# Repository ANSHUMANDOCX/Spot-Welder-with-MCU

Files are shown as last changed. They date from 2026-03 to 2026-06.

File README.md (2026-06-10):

# Spot Welder with MCU
## Description
- This is a Mosfet Based Spot welder made using IRFB7430 mosfet paired with a OLED display, rotary encoder and ATMEGA328P IC. This is a projet inspired by [This Project](https://www.instructables.com/DIY-Arduino-Battery-Spot-Welder/) 
- This is a two PCB Design and made such that one can order the PCB as a whole and has to separate the PCBs by Cutting manually to save cost.
- It has two Aluminum parts that attach to the PCB since the circuit will be dealing high current of about 400A in a single pulse
- The pulse timing can be adjusted using the rotary encode and is very simple to use.
- It has a onboard programmer for the ease of programming the board
- Flash using Arduino IDE with ATmega328P bootloader and 9600 baud rate
- The Code is not tested yet on my design
## Parts used 
- IRFB7430 Mosfet
- Atmega328p as the MCU 
- 0.96 128x64 oled display
- ABR-PR-12APBTX90 Amaron 12v 9Ah Battey for high short pulse current
- 6AWG wire to handle the high current
- 4010 fan 
- 2mm solid copper wire
## Usage guide 
We need to connect the GND of the Battery from the IN sign and connect to the U shaped aluminium portion followed by the rectangular aluminium block as one of the probes the other probe will the positive terminal of the battery.
## PCB Schematic and CAD 







## Build 
WhatsApp Image 2026-06-11 at 12 53 13 AM
WhatsApp Image 2026-06-11 at 12 53 09 AM
WhatsApp Image 2026-06-11 at 12 53 09 AM (1)
WhatsApp Image 2026-06-11 at 12 53 10 AM
WhatsApp Image 2026-06-11 at 12 53 10 AM (2)
WhatsApp Image 2026-06-11 at 12 53 10 AM (3)
WhatsApp Image 2026-06-11 at 12 53 11 AM (1)
WhatsApp Image 2026-06-11 at 12 53 11 AM (2)
https://drive.google.com/file/d/1lwMrrw48pk1E9WbPoM3kms2gutVuB4EL/view?usp=sharing

## BOM 
| Name | Purpose | Cost Per Item (USD) | Quantity | Total (USD) | Link | Distributor |
|---|---|---|---|---|---|---|
| SHIPPING JLC+LCSC | SHIPPING | 10.00 | 1 | 10.00 | [LINK](https://lcsc.com) | LCSC, JLC |
| Aluminum parts+ PCB | PCB + Aluminum Block | 6.00 | 1 | 6.00 | [LINK](https://jlccnc.com) | JLCCNC, JLCPCB  |
| FAN | to disspate heat | 0.70 | 1 | 0.70 | [LINK](https://makerbazar.in/products/generic-axial-dc-cooling-fan-blowers?variant=46306240004336) | Maker Bazar |
| Passive Component | Resistor diodes and Capacitor | 6.06 | 1 | 6.06 | [LINK](https://lcsc.com) | LCSC |
| 6AWG wire | Heavy duty wires | 4.73 | 1 | 4.73 | [LINK](https://makerbazar.in/products/flexible-silicon-wire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) | Maker Bazar |
| Battery 9ah | the battery | 18.25 | 1 | 18.25 | [LINK](https://www.flipkart.com/amaron-abr-pr-12apbtx90-9-ah-battery-bike/p/itmd23986a4bee47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,1,G,11214002,x,,,,,,,c,,,,,,,&entryMethod=22371611432&&cmpid=content_22371611432_gmc_pla&gad_campaignid=22371673895) | Flipkart |
| MCP1407-E/SN | gate driver | 1.75 | 1 | 1.75 | [LINK](https://www.lcsc.com/product-detail/C52138.html) | LCSC |
| 5.0SMDJ13A | diode | 0.42 | 4 | 1.70 | [LINK](https://www.lcsc.com/product-detail/C5295091.html) | LCSC |
| IRFB7430PBF(UMW) | Mosfets | 0.44 | 10 | 4.43 | [LINK](https://www.lcsc.com/product-detail/C19100591.html) | LCSC |
| CH340K | USB UART | 0.62 | 1 | 0.62 | [LINK](https://www.lcsc.com/product-detail/C968586.html) | LCSC |
| Oled | to show the timer | 2.17 | 1 | 2.17 | [LINK](https://www.lcsc.com/product-detail/C5248080.html) | LCSC |
| Rotary encoder | to set the timer | 1.42 | 1 | 1.42 | [LINK](https://www.lcsc.com/product-detail/C19712528.html) | LCSC |
| 3.3uH 20mΩ Inductor | Inductor | 0.71 | 1 | 0.71 | [LINK](https://www.lcsc.com/product-detail/C7588932.html) | LCSC |
| TPS563201DDCT | Regulator | 0.46 | 1 | 0.46 | [LINK](https://www.lcsc.com/product-detail/C2070819.html) | LCSC |
| ATMEGA328P-AU | MCU | 2.17 | 1 | 2.17 | [LINK](https://www.lcsc.com/product-detail/C14877.html) | LCSC |
| **Grand Total** | | | | **63.17** | | |

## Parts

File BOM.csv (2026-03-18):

Index | LCSC# | MPN | Manufacturer | Package | Customer # | Description | RoHS | Quantity | MOQ | Multiple | Unit Price($) | Extended Price($) | Product Link
1 | C14877 | ATMEGA328P-AU | MICROCHIP | TQFP-32(7x7) |  | AVR 8 Bit 20MHz 23 TQFP-32(7x7) Microcontrollers RoHS | yes | 1 | 1 | 1 | 2.3199 | 2.32 | https://www.lcsc.com/product-detail/C14877.html
2 | C2070819 | TPS563201DDCT | TI | TSOT-23-6 |  | Buck Switching Regulator IC Adjustable 0.768V~7V 1 Output 3A TSOT-23-6 | yes | 5 | 5 | 5 | 0.0959 | 0.48 | https://www.lcsc.com/product-detail/C2070819.html
3 | C7588932 | CMPI0640-3R3M | Ceaiya | SMD,7.2x6.6mm |  | 7.2A 3.3uH 8.5A 20mΩ Molded Inductor ±20% SMD,7.2x6.6mm Fixed Inductors RoHS | yes | 5 | 5 | 5 | 0.1418 | 0.71 | https://www.lcsc.com/product-detail/C7588932.html
4 | C19712528 | ED11305M-FB18.5A10-E20-160-G219 | CTR | DIP-5 |  | -30℃~+80℃ DIP-5 DIP Switches/SIP Switches RoHS | yes | 1 | 1 | 1 | 1.4161 | 1.42 | https://www.lcsc.com/product-detail/C19712528.html
5 | C5248080 | HS96L03W2C03 | HS | - |  | 0.96 128x64 SSD1315 chip I2C LCD, OLED, Graphic RoHS | yes | 1 | 1 | 1 | 2.1656 | 2.17 | https://www.lcsc.com/product-detail/C5248080.html
6 | C19100591 | IRFB7430PBF(UMW) | UMW | TO-220 |  | N-Channel 40V 409A 375W Through Hole TO-220 | yes | 10 | 1 | 1 | 0.4431 | 4.43 | https://www.lcsc.com/product-detail/C19100591.html
7 | C5295091 | 5.0SMDJ13A | JSCJ | SMCG |  | 21.5VC Clamp 232.6A Ipp TVS DIODE SMCG | yes | 4 | 1 | 1 | 0.4242 | 1.70 | https://www.lcsc.com/product-detail/C5295091.html
8 | C52138 | MCP1407-E/SN | MICROCHIP | SOP-8 |  | 4.5V~18V 6A 6A SOP-8 Gate Drivers RoHS | yes | 1 | 1 | 1 | 1.7547 | 1.75 | https://www.lcsc.com/product-detail/C52138.html
9 | C968586 | CH340K | WCH | ESSOP-10-150mil-1mm |  | USB to serial 2Mbps USB 2.0 ESSOP-10-150mil-1mm Interface Controllers RoHS | yes | 1 | 1 | 1 | 0.6221 | 0.62 | https://www.lcsc.com/product-detail/C968586.html
10 | C42428823 | RV2-3 | JIDC | - |  | 1.5~2.5 14~16 purple bronze Ring Connectors RoHS | yes | 10 | 10 | 10 | 0.0474 | 0.47 | https://www.lcsc.com/product-detail/C42428823.html
11 | C139746 | GB/T846-1985 KM3*10 | XHHD | - |  | Screws | - | 100 | 100 | 100 | 0.0021 | 0.21 | https://www.lcsc.com/product-detail/C139746.html
12 | C596861 | ABM3-16.000MHZ-D2Y-T | ABRACON | SMD5032-2P |  | Crystal 16MHz ±20ppm 18pF 40Ω SMD5032-2P | yes | 1 | 1 | 1 | 0.5689 | 0.57 | https://www.lcsc.com/product-detail/C596861.html
13 | C4747972 | RST1UF50V017 | KNSCHA | SMD,D4xL5.4mm |  | 1uF ±20% 50V Aluminum Electrolytic Capacitors 2000hrs@105℃ | yes | 20 | 20 | 20 | 0.0284 | 0.57 | https://www.lcsc.com/product-detail/C4747972.html
14 | C72517 | RVT1C471M0810 | ROQANG | SMD,D8xL10.2mm |  | 470uF ±20% 16V Aluminum Electrolytic Capacitors 2000hrs@105℃ | yes | 10 | 10 | 10 | 0.0544 | 0.54 | https://www.lcsc.com/product-detail/C72517.html
15 | C14663 | CC0603KRX7R9BB104 | YAGEO | 0603 |  | 100nF ±10% 50V Ceramic Capacitor X7R 0603 | yes | 100 | 100 | 100 | 0.0028 | 0.28 | https://www.lcsc.com/product-detail/C14663.html
16 | C100042 | CC0603KRX7R9BB103 | YAGEO | 0603 |  | 10nF ±10% 50V Ceramic Capacitor X7R 0603 | yes | 100 | 100 | 100 | 0.0024 | 0.24 | https://www.lcsc.com/product-detail/C100042.html
17 | C22978 | 0603WAF3301T5E | UNI-ROYAL | 0603 |  | 3.3kΩ ±1% 100mW 0603 Thick Film Resistor | yes | 100 | 100 | 100 | 0.0015 | 0.15 | https://www.lcsc.com/product-detail/C22978.html
18 | C2907058 | FRC0603F6200TS | FOJAN | 0603 |  | 620Ω ±1% 100mW 0603 Thick Film Resistor | yes | 100 | 100 | 100 | 0.0013 | 0.13 | https://www.lcsc.com/product-detail/C2907058.html
19 | C22548 | RC0603FR-071KL | YAGEO | 0603 |  | 100mW 1kΩ 75V Thick Film Resistor ±100ppm/℃ ±1% 0603 Chip Resistor - Surface Mount RoHS | yes | 100 | 100 | 100 | 0.0013 | 0.13 | https://www.lcsc.com/product-detail/C22548.html
20 | C2930423 | FRC1206F30R0TS | FOJAN | 1206 |  | 30Ω ±1% 250mW 1206 Thick Film Resistor | yes | 100 | 100 | 100 | 0.0034 | 0.34 | https://www.lcsc.com/product-detail/C2930423.html
21 | C2910053 | MMSZ4687 | JSCJ | SOD-123 |  | Zener Diode Independent 4.3V 350mW Surface Mount SOD-123 | yes | 20 | 20 | 20 | 0.0260 | 0.52 | https://www.lcsc.com/product-detail/C2910053.html
22 | C2500 | BAV99,215 | Nexperia | SOT-23 |  | Diode Array 1 Pair Series Connection 100V 215mA Surface Mount SOT-23 | yes | 20 | 50 | 50 | 0.0168 | 0.34 | https://www.lcsc.com/product-detail/C2500.html
23 | C148214 | SMAJ13A | Littelfuse | DO-214AC(SMA) |  | 21.5VC Clamp 18.6A Ipp TVS DIODE DO-214AC(SMA) | yes | 10 | 5 | 5 | 0.1177 | 1.18 | https://www.lcsc.com/product-detail/C148214.html
24 | C98220 | RC0603FR-0710KL | YAGEO | 0603 |  | 100mW 10kΩ 75V Thick Film Resistor ±100ppm/℃ ±1% 0603 Chip Resistor - Surface Mount RoHS | yes | 100 | 100 | 100 | 0.0013 | 0.13 | https://www.lcsc.com/product-detail/C98220.html
25 | C23080 | 0603WAF5622T5E | UNI-ROYAL | 0603 |  | 56.2kΩ ±1% 100mW 0603 Thick Film Resistor | yes | 100 | 100 | 100 | 0.0014 | 0.14 | https://www.lcsc.com/product-detail/C23080.html

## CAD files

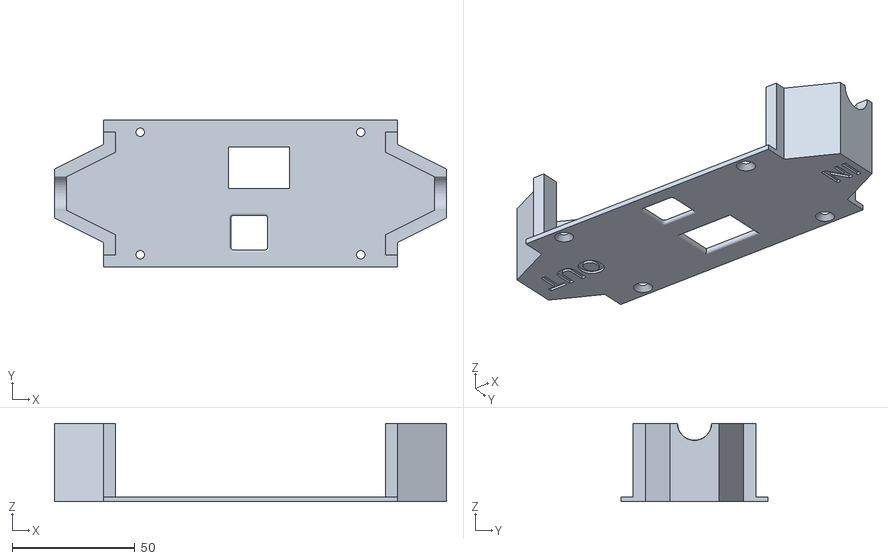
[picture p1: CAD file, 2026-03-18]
CAD/TOP PART_.stl
160.0 x 60.0 x 32.0

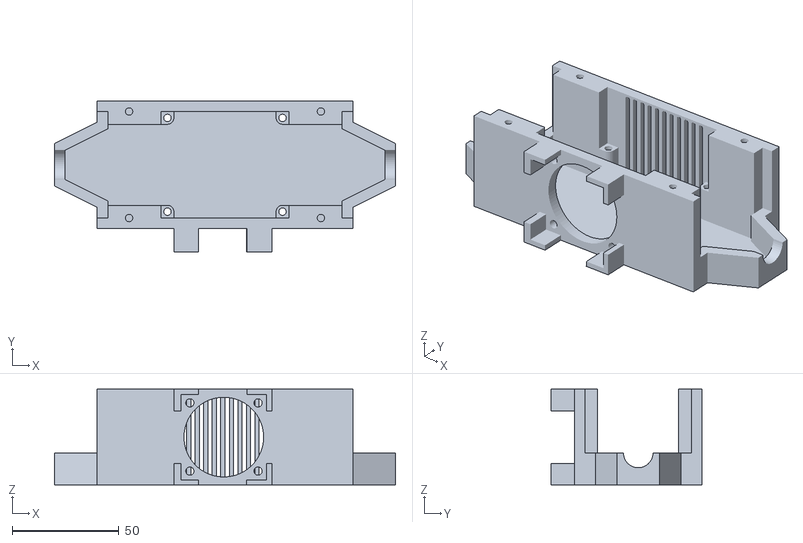
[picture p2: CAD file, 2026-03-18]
CAD/BOTTOM PART SPOT.stl
160.0 x 71.0 x 45.0

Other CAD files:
CAD/BOTTOM PART SPOT.f3z
CAD/Top part.f3d

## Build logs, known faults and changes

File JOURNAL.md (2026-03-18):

<!--
  This journal is auto generated by Stasis.
-->

# 3/18/2026 6 PM - worked on cad

_Time spent: 1h_

made it look better added lables along with improved the fan housing and added screw holes so that the fan hold better








# 3/18/2026 1 PM - Added mousebites

_Time spent: 0.5h_

added mousebites to the board to make it cost efficient 








# 3/18/2026 12 PM - some edits

_Time spent: 0.75h_

Arranged the Schematic to look clean 

added a pin to connect fan and added silkscreens for the respective pins








# 3/18/2026 10 AM - Added fan and some edits

_Time spent: 1.5h_

Added housing fro the fan along with filleting edges and holes for the thick wires comming out of the housing also added the air vents since those mosfets get very hot 











# 3/17/2026 8 PM - half done CAD

_Time spent: 3h_

Started out and made to midway to the cad made the top and bottom parts but still need more polishing 








# 3/17/2026 6 PM - Completed the PCB Routing

_Time spent: 2h_

Completed the Routing along with assigning the 3d parts to the components respectively








# 3/17/2026 1 PM - Started out with PCB routing

_Time spent: 3h_

Assigned the footprints to all the components 

Started out with the PCb and completed the MOSFET board as per the guide the system will be a two piece model 

took a lot of time since i needed to perfect the measurements for since i need to attach aluminium parts to the board so it can handel high current








# 3/16/2026 9 PM - Finding the right battery

_Time spent: 1h_

i was looking out for the best battery that is good for this and aswell under the budget i finally went with [this ](https://www.flipkart.com/amaron-abr-pr-12apbtx90-9-ah-battery-bike/p/itmd23986a4bee47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,1,G,11214002,x,,,,,,,c,,,,,,,&entryMethod=22371611432&&cmpid=content_22371611432_gmc_pla&gad_campaignid=22371673895) one since it has a good enough cold crank current of 380A








# 3/16/2026 8 PM - Almost done with the schematic and researched for parts

_Time spent: 3h_

I am following this [guide](https://www.instructables.com/DIY-Arduino-Battery-Spot-Welder/) however i will be the MCU to make it completly based on the board along with adding a buzzer 
Also i will be using a 12v 18ah battery to go along with it along with 6 awg wires to use with the complete system 








# 3/15/2026 7 PM - Started out with the Schematic

_Time spent: 2.5h_

Started out with the schematic i will be making a controller circuit for the system where i iwll be adding a oled display along with a rotary encoder to set the turn on time. I will be making it off a ATMEGA328p paired with a CH340K ic and type c input to program the boards.

Also it was my first time i used TI Webench for finding the right regulator ic for the atmega328p. 








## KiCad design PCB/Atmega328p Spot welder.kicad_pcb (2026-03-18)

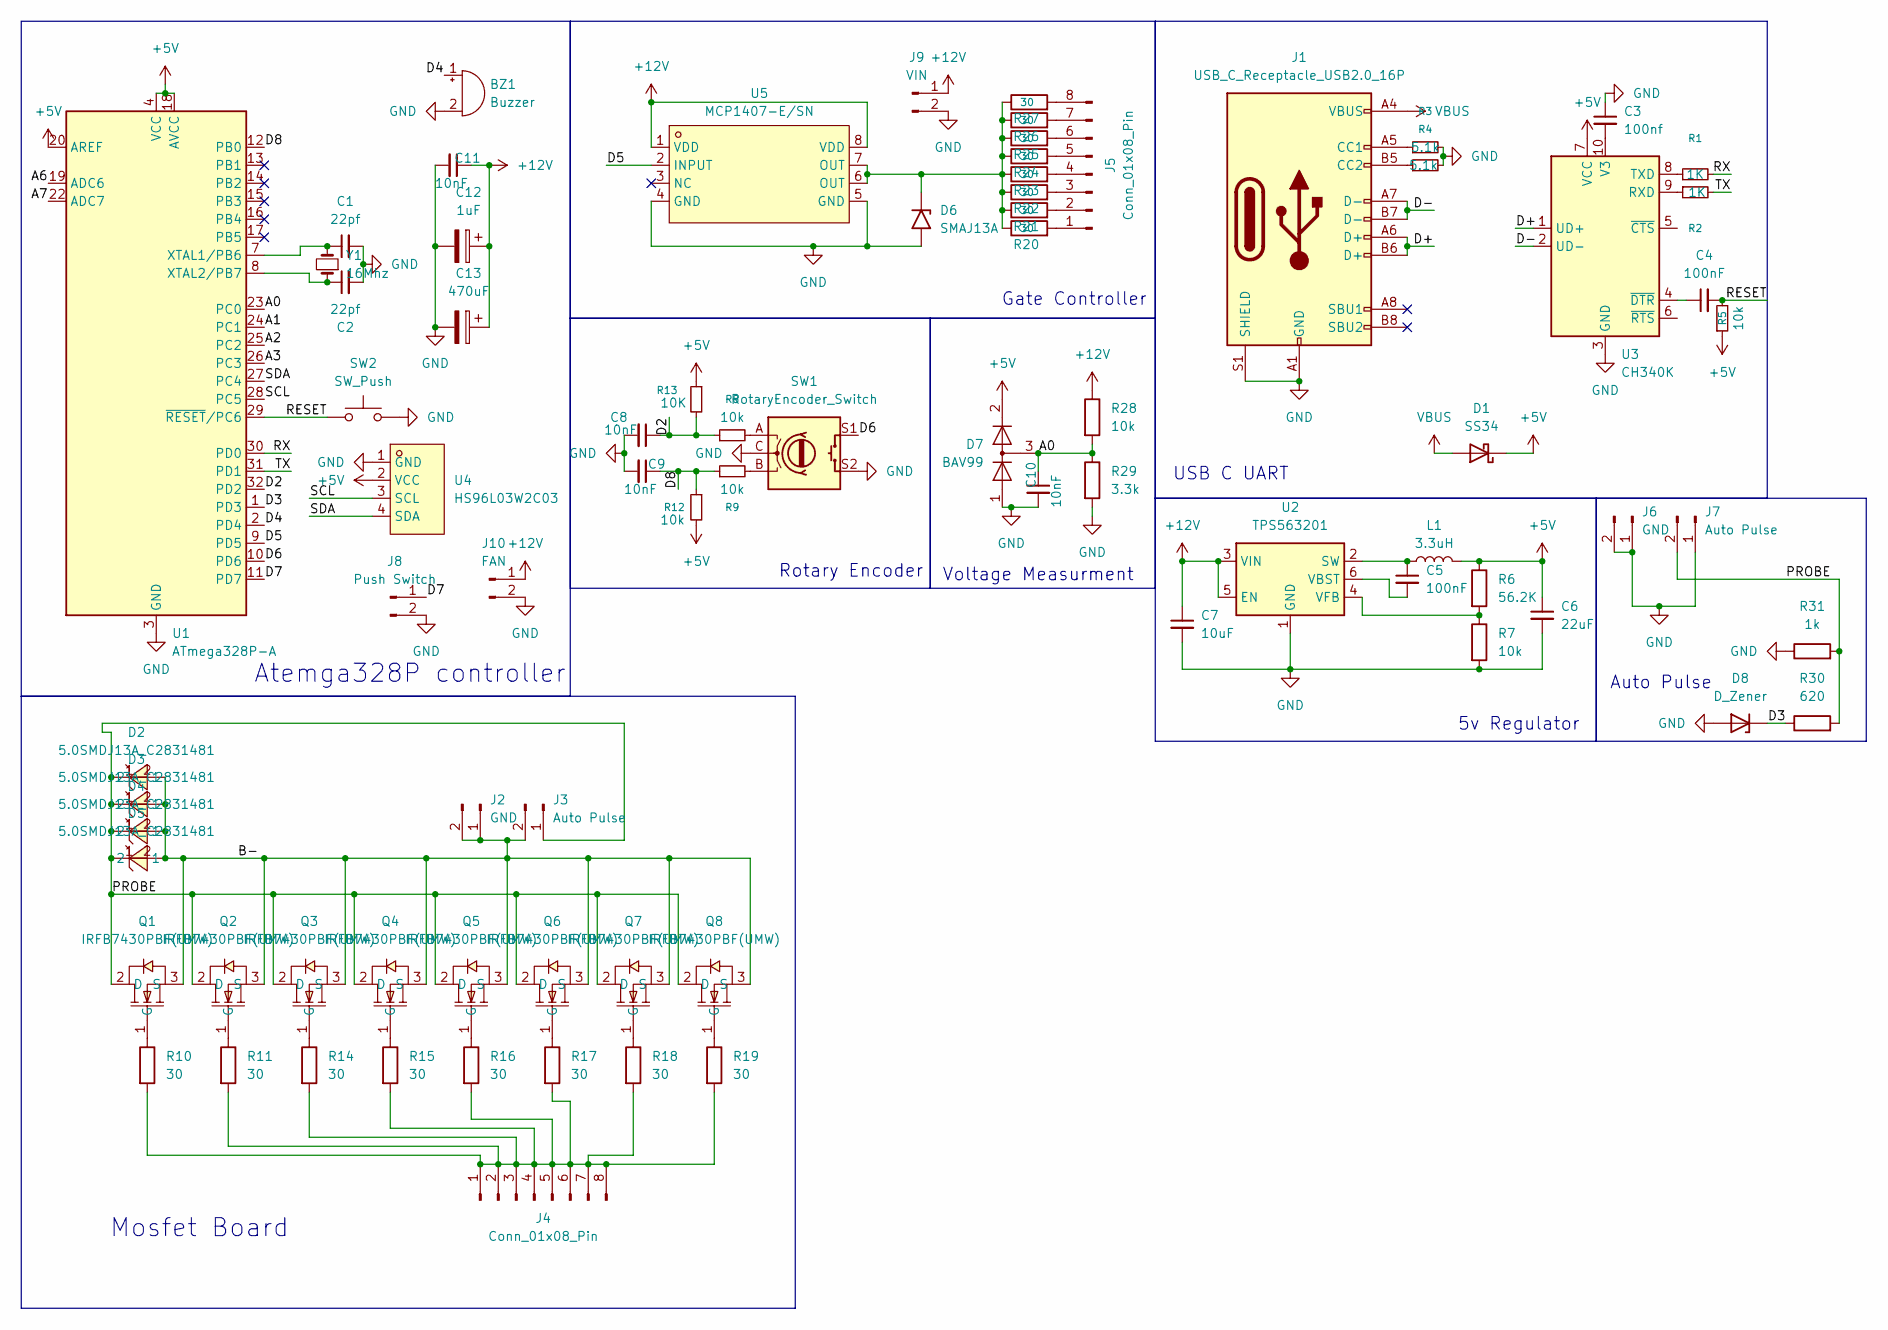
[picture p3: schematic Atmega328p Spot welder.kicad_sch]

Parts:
BZ1: Buzzer; Buzzer_12x9.5RM7.6
C1, C2: 22pf; C_0603_1608Metric
C3: 100nf; C_0603_1608Metric
C4, C5: 100nF; C_0603_1608Metric
C6: 22uF; C_0603_1608Metric
C7: 10uF; C_0603_1608Metric
C8, C9, C10, C11: 10nF; C_0603_1608Metric
C12: 1uF; CP_Elec_4x5.4
C13: 470uF; CP_Elec_8x10.5
D1: SS34; D_SMA
D2, D3, D4, D5: 5.0SMDJ13A_C2831481; SMC_L6.9-W5.9-LS8.0-RD; LCSC Part C2831481
D6: SMAJ13A; D_SMA
D7: BAV99; SOT-23
D8: D_Zener; D_SOD-123
J1: USB_C_Receptacle_USB2.0_16P; USB_C_Receptacle_HCTL_HC-TYPE-C-16P-01A
J2, J6: GND; PinHeader_1x02_P2.54mm_Vertical
J3, J7: Auto Pulse; PinHeader_1x02_P2.54mm_Vertical
J4, J5: Conn_01x08_Pin; PinHeader_1x08_P2.54mm_Vertical
J8: Push Switch; PinHeader_1x02_P2.54mm_Vertical
J9: VIN; PinHeader_1x02_P2.54mm_Vertical
J10: FAN; PinHeader_1x02_P2.54mm_Vertical
L1: 3.3uH; L_Bourns_SRP7028A_7.3x6.6mm
Q1, Q2, Q3, Q4, Q5, Q6, Q7, Q8: IRFB7430PBF(UMW); TO-220-3_Horizontal_TabDown; LCSC Part C19100591
R1, R2: 1K; C_0603_1608Metric
R3, R4: 5.1k; C_0603_1608Metric
R5, R7, R8, R9, R12, R28: 10k; C_0603_1608Metric
R6: 56.2K; C_0603_1608Metric
R10, R11, R14, R15, R16, R17, R18, R19, R20, R21, R22, R23, R24, R25, R26, R27: 30; R_1206_3216Metric
R13: 10K; C_0603_1608Metric
R29: 3.3k; C_0603_1608Metric
R30: 620; C_0603_1608Metric
R31: 1k; C_0603_1608Metric
SW1: RotaryEncoder_Switch; RotaryEncoder_Alps_EC11E_Vertical_H20mm_CircularMountingHol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
SW2: SW_Push; SW_Push_SPST_NO_Alps_SKRK
U1: ATmega328P-A; TQFP-32_7x7mm_P0.8mm
U2: TPS563201; SOT-23-6
U3: CH340K; SSOP-10-1EP_3.9x4.9mm_P1mm_EP2.1x3.3mm
U4: HS96L03W2C03; OLED-TH_L27.8-W27.2-P2.54_C9900033791; LCSC Part C5248080
U5: MCP1407-E/SN; SOP-8_L4.9-W3.9-P1.27-LS6.0-BL; LCSC Part C52138
Y1: 16Mhz; Crystal_SMD_5032-2Pin_5.0x3.2mm

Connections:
+5V: C6.1, D1.1 (K), D7.2 (A), L1.2, R5.1, R6.1, R12.2, R13.1, U1.4 (VCC), U1.6 (VCC), U1.18 (AVCC), U1.20 (AREF), U3.7 (VCC), U4.2 (VCC)
+12V: C7.1, C11.1, C12.1, C13.1, J9.1, J10.1, R28.1, U2.3 (VIN), U2.5 (EN), U5.1 (VDD), U5.8 (VDD)
/A0: C10.1, D7.3 (K), R28.2, R29.1, U1.23 (PC0)
/A1: U1.24 (PC1)
/A2: U1.25 (PC2)
/A3: U1.26 (PC3)
/A6: U1.19 (ADC6)
/A7: U1.22 (ADC7)
/B-: D2.2, D3.2, D4.2, D5.2, J2.1, J2.2, J3.2, Q1.3 (S), Q2.3 (S), Q3.3 (S), Q4.3 (S), Q5.3 (S), Q6.3 (S), Q7.3 (S), Q8.3 (S)
/D2: C8.1, R8.1, R13.2, U1.32 (PD2)
/D3: D8.1 (K), R30.1, U1.1 (PD3)
/D4: BZ1.1 (+), U1.2 (PD4)
/D5: U1.9 (PD5), U5.2 (INPUT)
/D6: SW1.S1, U1.10 (PD6)
/D7: J8.1, U1.11 (PD7)
/D8: C9.1, R9.1, R12.1, U1.12 (PB0)
/D+: J1.A6 (D+), J1.B6 (D+), U3.1 (UD+)
/D-: J1.A7 (D-), J1.B7 (D-), U3.2 (UD-)
/PROBE: D2.1, D3.1, D4.1, D5.1, J3.1, J7.2, Q1.2 (D), Q2.2 (D), Q3.2 (D), Q4.2 (D), Q5.2 (D), Q6.2 (D), Q7.2 (D), Q8.2 (D), R30.2, R31.2
/RESET: C4.2, R5.2, SW2.1, U1.29 (~RESET/PC6)
/RX: R1.2, U1.30 (PD0)
/SCL: U1.28 (PC5), U4.3 (SCL)
/SDA: U1.27 (PC4), U4.4 (SDA)
/TX: R2.2, U1.31 (PD1)
GND: BZ1.2 (-), C1.2, C2.2, C3.1, C6.2, C7.2, C8.2, C9.2, C10.2, C11.2, C12.2, C13.2, D6.2 (A2), D7.1 (K), D8.2 (A), J1.A1 (GND), J1.A12 (GND), J1.B1 (GND), J1.B12 (GND), J1.S1 (SHIELD), J6.1, J6.2, J7.1, J8.2, J9.2, J10.2, R3.2, R4.2, R7.2, R29.2, R31.1, SW1.C, SW1.S2, SW2.2, U1.3 (GND), U1.5 (GND), U1.21 (GND), U2.1 (GND), U3.3 (GND), U3.11 (GND), U4.1 (GND), U5.4 (GND), U5.5 (GND)
unnamed: D6.1 (A1), R20.1, R21.1, R22.1, R23.1, R24.1, R25.1, R26.1, R27.1, U5.6 (OUT), U5.7 (OUT)
unnamed: J1.A5 (CC1), R3.1
unnamed: J1.B5 (CC2), R4.1
unnamed: J4.1, J4.2, J4.3, J4.4, J4.5, J4.6, J4.7, J4.8, R10.2, R11.2, R14.2, R15.2, R16.2, R17.2, R18.2, R19.2
unnamed: J5.1, R20.2
unnamed: J5.2, R21.2
unnamed: J5.3, R22.2
unnamed: J5.4, R23.2
unnamed: J5.5, R24.2
unnamed: J5.6, R25.2
unnamed: J5.7, R26.2
unnamed: J5.8, R27.2
unnamed: Q1.1 (G), R10.1
unnamed: Q2.1 (G), R11.1
unnamed: Q3.1 (G), R14.1
unnamed: Q4.1 (G), R15.1
unnamed: Q5.1 (G), R16.1
unnamed: Q6.1 (G), R17.1
unnamed: Q7.1 (G), R18.1
unnamed: Q8.1 (G), R19.1
unnamed: R8.2, SW1.A
unnamed: R9.2, SW1.B
unnamed: C1.1, U1.7 (XTAL1/PB6), Y1.2
unnamed: C2.1, U1.8 (XTAL2/PB7), Y1.1
unnamed: C5.1, L1.1, U2.2 (SW)
unnamed: C5.2, U2.6 (VBST)
unnamed: R6.2, R7.1, U2.4 (VFB)
unnamed: R2.1, U3.9 (RXD)
unnamed: R1.1, U3.8 (TXD)
unnamed: C3.2, U3.10 (V3)
unnamed: C4.1, U3.4 (~DTR)
VBUS: D1.2 (A), J1.A4 (VBUS), J1.A9 (VBUS), J1.B4 (VBUS), J1.B9 (VBUS)

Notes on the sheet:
5v Regulator
Rotary Encoder
Auto Pulse
Mosfet Board
Voltage Measurment
Gate Controller
USB C UART
Atemga328P controller

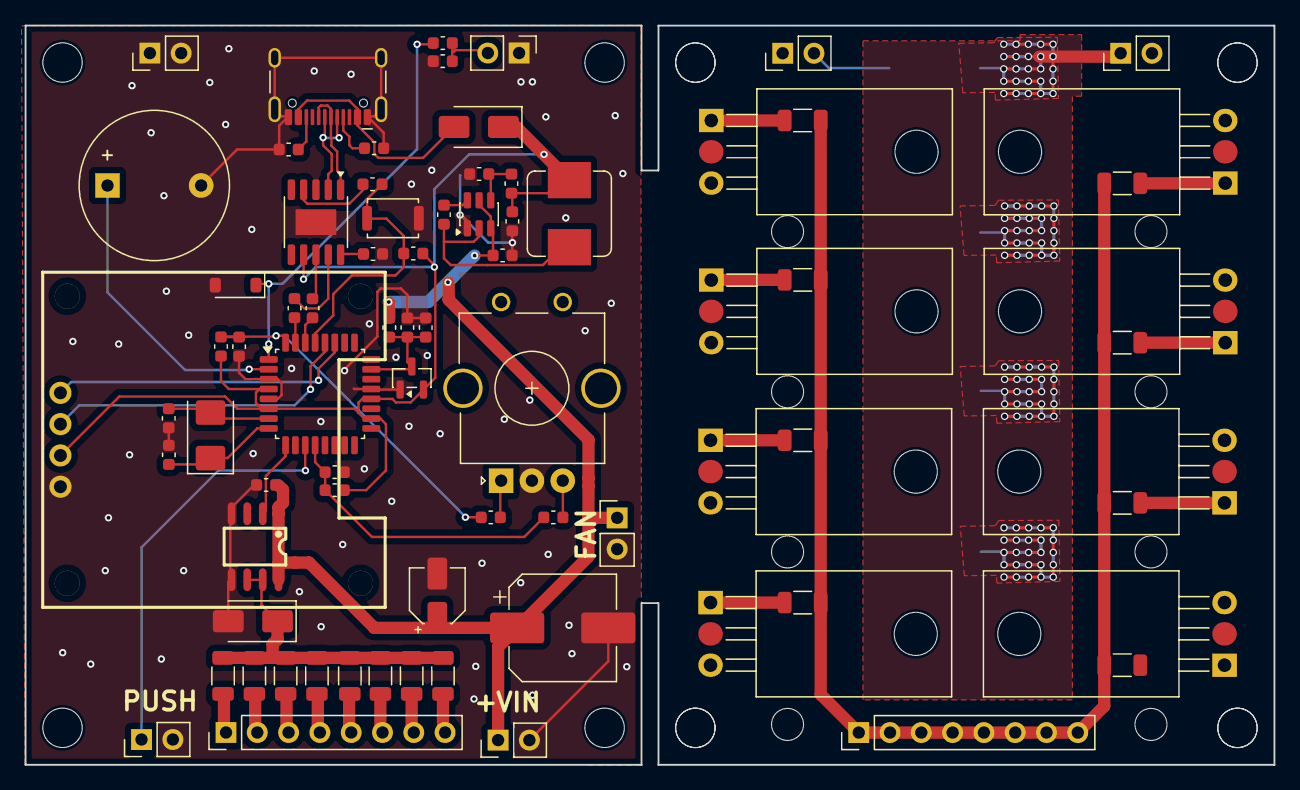
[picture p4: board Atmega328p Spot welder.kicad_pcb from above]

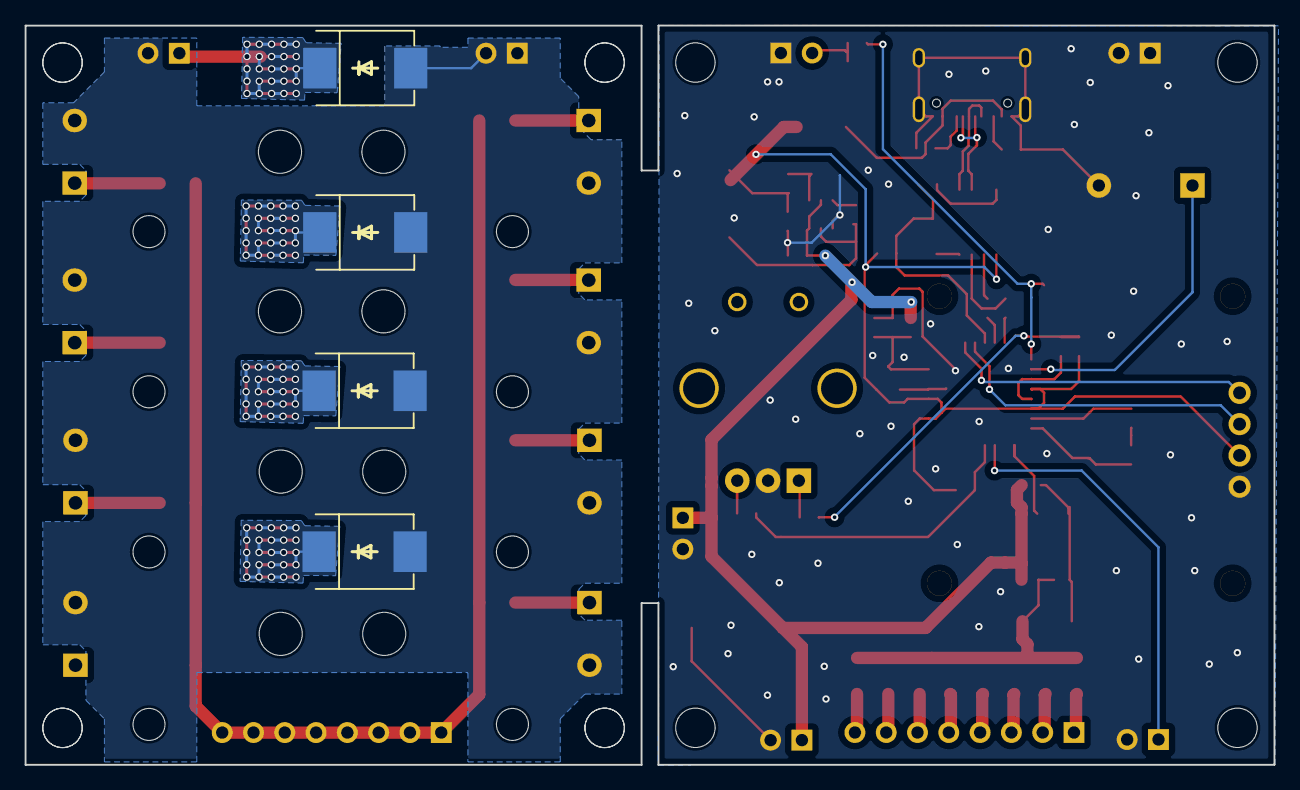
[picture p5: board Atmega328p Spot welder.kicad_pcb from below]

Board: 2 copper layers, 101.4 x 60.0 mm, 80 parts (4 on the bottom side), 51 nets.

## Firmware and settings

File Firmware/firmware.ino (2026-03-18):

#define _ARDUINO_SPOT_WELDER_V3_3_5
/***********************************************************************************************//**
 *  \par        Arduino Spot Welder - Source File.
 *
 *  \par        Details
 *  \par
 *              Arduino Spot Welder V3 firmware.
 *              This is the Arduino Code for the Spot Welder V3. Do not use it with the older V2
 *              pcbs. It is not compatible with these.
 *  \par
 *              You need to have the Adafruit_GFX library and the Adafruit_SSD1306 library
 *              installed in your Arduino IDE to sucessfully compile the Code.
 *
 *              This release has been tested with the following library versions:
 *              Adafruit SSD1306 V2.5.13
 *              Adafruit GFX V1.12.0 
 *
 *  \file       Arduino_Spot_Welder_V3_3_5.ino
 *  \author     Marc Schönfleisch <http://malectrics.eu/>
 *  \version    3.3.5
 *  \date       April 2025
 *  \copyright  Copyright(c)2025 Marc Schönfleisch <info@malectrics.eu>. All right reserved.
 *
 *  \par        Changelog
 *  \li         01jul2017  MS  Initial release
 *  \li         12dec2017  JFF New release with major rewrite
 *  \li         15jan2018  MS change battery voltage reading for V3.2 Spot Welder
 *  \li         05jun2018  MS remove softwarereset to eliminate need of optiboot bootloader
 *  \li         11aug2018  MS fix 10.000 welds counter bug
 *  \li         24nov2018  AJ improve Auto Pulse functionality with progress bar
 *  \li         09apr2019  MS add foot switch wrong connection error message
 *  \li         05jun2019  MS code update for SSD1306 library V1.2.9 and general improvements
 *  \li         12sep2019  GW imporove slow progress bar drawing problem
 *  \li         01apr2020  RS fix 10.000 welds count limit
 *  \li         03apr2020  MS add overvoltage alarm
 *  \li         09apr2025  MS improve measured voltage offset calibration
 *
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
 *//***********************************************************************************************/

/***********************************************************************************************//**
 *  \par        Menu and display Screen Descriptions.
 *              The main screen is accessed by a normal device boot. The initial screen is raised
 *              unless the input voltage is too low, in which case a low voltage screen is raised.
 *              The menus and dispay screens are arranged as follows;
 *  \verbatim
 +----------------+  MAIN SCREEN
 |   Status Line  |  Trigger mode, number of welds, battery charge indicator
 |----------------|
 | Variable       |  Pulse duration in 4x font, adjusted using the encoder
 | Variable Units |  Time units in 2x font
 |    Message     |  Message line in 1x font
 +----------------+

 +----------------+  MAIN MENU
 |   Status Line  |  Trigger mode, number of welds, battery charge indicator
 |----------------|
 |   Auto Pulse   |  Raise the AutoPulse menu
 |   Batt Alarm   |  Raise the Battery Alarm setting screen
 |   Shrt Pulse   |  Raise the Short Pulse setting screen
 +----------------+

 +----------------+  AUTOPULSE MENU
 |  Auto Pulse    |  Menu label
 |----------------|
 |   Activate     |  Raise the AutoPulse Activate setting screen
 |    Delay       |  Raise the AutoPulse Delay setting screen
 |     Exit       |  Exit to the Main screen
 +----------------+

    The system screen is accessed by booting the device with the encoder push button depressed.
    The screen allows changing of system settings. It is arranged as follows;

 +----------------+  SYSTEM MENU
 |    Settings    |  Raise the SETTINGS menu
 |    Display     |  Raise the Display Invert setting screen
 |     Boot       |  Raise the REBOOT menu
 +----------------+

 +----------------+  SETTINGS MENU
 |   Max Pulse    |  Raise the Maximum Weld Pulse Duration setting screen
 |   Batt Cal     |  Raise the Battery Calibration screen
 |     Exit       |  Return to the System Menu
 +----------------+

 +----------------+  REBOOT MENU
 |     Reboot     |  Re-boot device
 |   Safe Reset   |  Reset EEPROM keeping current weld count and re-boot the device
 |   Full Reset   |  Reset EEPROM to factory default settings and re-boot the device
 +----------------+
    \endverbatim
 *//***********************************************************************************************/

#include <Arduino.h>
#include <SPI.h>
#include <Wire.h>
#include <avr/wdt.h>
#include <Adafruit_GFX.h>
#include <gfxfont.h>
#include <Adafruit_SSD1306.h>
#include <EEPROM.h>
#include "printf.h"
#include "Arduino_Spot_Welder_V3_3_5.h"

// Machine states
enum states {
	ST_STANDBY,        /**< Machine state: standby */
	ST_MAIN_SCREEN,    /**< Machine state: display main screen */
	ST_MAIN_SCREEN_CNT, /**< Machine state: display statistics */
	ST_MENU_SCREEN,    /**< Machine state: display menu screen */
	ST_SUB_MENU_1,     /**< Machine state: display sub-menu1 */
	ST_SUB_MENU_2,     /**< Machine state: display sub-menu2 */
	ST_BATTERY_LOW,    /**< Machine state: low battery voltage */
  ST_BATTERY_HIGH,   /**< Machine state: high battery voltage */

	ST_SYSTEM_SCREEN,  /**< Machine state: display system screen */
	ST_SYSTEM_MENU,    /**< Machine state: display system menu */
	ST_SETTINGS_MENU,  /**< Machine state: display settings menu */
	ST_REBOOT_MENU,    /**< Machine state: display reboot menu */
	ST_MAXWELD_SCREEN, /**< Machine state: display max weld setting screen */
	ST_BATTCAL_SCREEN, /**< Machine state: display battery calibration */
	ST_INVERT_SCREEN,  /**< Machine state: display invert setting screen */
	ST_PULSE_VOLTAGE,  /**< Machine state: display measured pulse voltage screen */
};

enum event {
	// Private machine events
	EV_NONE,           /**< Machine event: no pending event */
	EV_BTNDN,          /**< Machine event: button pressed */
	EV_BTNUP,          /**< Machine event: button released */
	EV_ENCUP,          /**< Machine event: encoder rotate right */
	EV_ENCDN,          /**< Machine event: encoder rotate left */

	// Public machine events
	EV_BOOTDN,         /**< Machine event: button pressed on boot */
	EV_STBY_TIMEOUT,   /**< Machine event: standby timer has timed out */
	EV_BATT_LV,        /**< Machine event: battery low voltage event */
  EV_BATT_HV,        /**< Machine event: battery high voltage event */
	EV_EEUPD,          /**< Machine event: EEPROM needs updating */
	EV_PULSE_VOLTS,    /**< Machine event: foot switch hold during pulse */
};

/***************************************************************************************************
* Global program variables and objects                                                             *
***************************************************************************************************/

// Structures and objects
progData pData;                             /**< Program operating data */
Adafruit_SSD1306 display( 128, 64, &Wire, OLED_RESET, 800000L ); /**< OLED display object */

// Static variables
uint8_t mState         = ST_MAIN_SCREEN;    /**< Current machine state */
uint8_t batteryVoltage = DEF_NOM_BATT_V;    /**< Current battery voltage x10 */
uint8_t rawbatteryVoltage = DEF_NOM_BATT_V;    /**< Current battery voltage x10, raw measured without offset */
int8_t batt_gauge;                          /**< Battery gauge segments to display */
boolean sysMenu = false;             /**< In the system menu structure */

// Volatile variables - will be changed by the ISR
volatile unsigned long lastActiveTime;
volatile uint8_t mEvent;          /**< Current pending machine event */

void reset_mcusr( void ) __attribute__( ( naked ) ) __attribute__( ( section( ".init3" ) ) );
void reset_mcusr( void ) {
	MCUSR = 0;
	wdt_disable();
}

/***************************************************************************************************
* Program setup                                                                                    *
***************************************************************************************************/
/**
 *  \brief    Program setup.
 *  \remarks  Performed once only at powerup.
 */
void setup() {
#if defined  _DEVELOPMENT_ || defined _BOOTSYS_
		Serial.begin( _SERIAL_BAUD_ );
#endif /* _DEVELOPMENT_ || _BOOTSYS_*/

	// Setup the pin states and directions.
	pinMode( PIN_LED,              OUTPUT );
	pinMode( PIN_PULSE,            OUTPUT );
	pinMode( PIN_CLK,              INPUT );
	pinMode( PIN_DT,               INPUT );
	pinMode( PIN_SW,               INPUT_PULLUP );
	pinMode( PIN_FOOT_SWITCH,      INPUT_PULLUP );
	pinMode( PIN_AUTO_PULSE,       INPUT );
	digitalWrite( PIN_SW,          HIGH );
	digitalWrite( PIN_FOOT_SWITCH, HIGH );

	// Setup the OLED display and clear it.
	display.begin( SSD1306_SWITCHCAPVCC, 0x3C );
	display.clearDisplay(); // clear remnants when rebooting
	display.display();

	// The interrupt is used to sense the encoder rotation. It could just as well be polled
	// without loss of responsiveness. This was actually tried and no noticeable performance
	// degradation was observed. Interrupts are usefull for high speed encoders such as
	// used on servo systems. Manually adjusted encoders are very slow.
	attachInterrupt( ENC_INT, isr, FALLING );

	// This is used by the standbby timer to identify the period of inactivity.
	lastActiveTime = millis();

	// Test if the pushbutton is pressed at boot time. If so then ensure entry to the system
	// menu by the issue of a boot button down event.
#ifdef _BOOTSYS_
		mEvent = EV_BOOTDN;
#else
		mEvent = btnState() == B_DN ? EV_BOOTDN : EV_NONE;
#endif /* _BOOTSYS_ */

	loadEeprom();

	// Invert the display if required and draw the splash screen. This can only be done after
	// loading the program data (which contains the screen invert switch).
	display.setRotation( pData.pFlags.en_oledInvert ? OLED_INVERT : 0 );
	splash();

	if ( !digitalRead( PIN_FOOT_SWITCH ) )
		foot_switch_error();

  batteryVoltage = DEF_NOM_BATT_V;

#ifdef _DEVELOPMENT_
		Serial.print( F( "Pulse Time       " ) ); Serial.println( pData.pulseTime );
		Serial.print( F( "Pulse Voltage    " ) ); Serial.println( pData.PulseBatteryVoltage );
		Serial.print( F( "Pulse Amps       " ) ); Serial.println( pData.PulseAmps );
		Serial.print( F( "Battery Alarm    " ) ); Serial.println( pData.batteryAlarm );
		Serial.print( F( "Weld Count       " ) ); Serial.println( pData.weldCount );
		Serial.print( F( "Auto Pulse Delay " ) ); Serial.println( pData.autoPulseDelay );
		Serial.print( F( "Max Pulse Time   " ) ); Serial.println( pData.maxPulseTime );
		Serial.print( F( "Short Pulse Time " ) ); Serial.println( pData.shortPulseTime );
		Serial.print( F( "Battery Offset   " ) ); Serial.println( pData.batteryOffset );
		Serial.print( F( "Auto Pulse       " ) ); Serial.println( pData.pFlags.en_autoPulse ? "On" : "Off" );
		Serial.print( F( "Display Invert   " ) ); Serial.println( pData.pFlags.en_oledInvert ? "Invert" : "Normal" );
#endif /* _DEVELOPMENT_ */
}

/***************************************************************************************************
* Main program loop                                                                                *
***************************************************************************************************/
/**
 *  \brief    Main program loop.
 *  \remarks  Manages the state machine and eeprom updates.
 */
void loop() {
	// The state machine is run every loop cycle - as fast as possible.
	stateMachine();

	// The eeprom is updated with changed variables. The update routine internally ensures that
	// the eeprom is only updated every few seconds to limit wearout.
	updateEeprom();
}

/***************************************************************************************************
* State Machine                                                                                    *
***************************************************************************************************/
/**
 *  \brief  Implementation of state machine.
 */

// This entire state machine is legacy code that has been much modified and added to. It is
// somewhat of a "dog's breakfast" and really is in need of a complete rewrite. Even I have
// difficulty following it and modifications that work are a pleasant surprise - JFF.

void stateMachine() {
	char str[5];
	static uint8_t selectedMenu       = 0;
	static uint8_t selectedMainMenu   = 0;
	static uint8_t selectedSubMenu    = 0;
	static boolean btn                = false;
	static uint8_t measuredVoltage;

	// Scan for events - the event queue length is one.

	// Process any public boot events. These events are the highest priority
	// and must be processed before any of the private events.
	if ( mEvent == EV_BOOTDN ) {
		mState = ST_SYSTEM_SCREEN;
		mEvent = EV_NONE;

	} else {
		// Search for and process any private events.
		checkForBtnEvent();
		checkForSleepEvent();
		checkForLowVoltageEvent();

		switch ( mEvent ) {
		case EV_STBY_TIMEOUT: mState = ST_STANDBY;
			mEvent = EV_NONE;
			break;
		case EV_BATT_LV:

			if ( !sysMenu ) mState = ST_BATTERY_LOW;

			mEvent = EV_NONE;
			break;
    case EV_BATT_HV:

      if ( !sysMenu ) mState = ST_BATTERY_HIGH;

      mEvent = EV_NONE;
      break;
		case EV_BTNUP:

			if ( mState != ST_REBOOT_MENU ) mEvent = EV_NONE;

			break;
		case EV_PULSE_VOLTS: mState = ST_PULSE_VOLTAGE;
			mEvent = EV_NONE;
			break;
		}
	}

	// Machine states
	switch ( mState ) {

	// Pulse Voltage State entered by holding down the foot switch button during pulse,
	// it is exited by a button press event.
	case ST_PULSE_VOLTAGE:

		if ( mEvent == EV_BTNDN )
			mState = sysMenu ? ST_SYSTEM_SCREEN : ST_MAIN_SCREEN;

		displayPulseData();
		mEvent = EV_NONE;
		break;

	// Standby state entered by receiving a standby timeout event,
	// it is exited by a button press event.
	case ST_STANDBY:

		if ( mEvent == EV_BTNDN ) mState = sysMenu ? ST_SYSTEM_SCREEN : ST_MAIN_SCREEN;

		message( FPSTR( LS_STANDBY ), FPSTR( LS_CLICKBTN ), FPSTR( LS_EXITSTBY ) );
		mEvent = EV_NONE;
		break;

	// Low battery state. Entered by receiving a low battery event,
	// this state cannot be exited by clicking the rotary encoder
	case ST_BATTERY_LOW:

		if ( mEvent == EV_BTNDN ) mState = sysMenu ? ST_SYSTEM_SCREEN : ST_MAIN_SCREEN;

		displayLowBattery();
		mEvent = EV_NONE;
		break;

      // Overvoltage battery state. Entered by receiving a high battery event,
  // this state cannot be exited except by reboot.
  case ST_BATTERY_HIGH:

    if ( mEvent == EV_BTNDN ) mState = sysMenu ? ST_SYSTEM_SCREEN : ST_MAIN_SCREEN;

    displayHighBattery();
    mEvent = EV_NONE;
    break;

	// Main screen state displays the main screen without responding to events. This is
	// effectively the home location for an idle loop that cycles through this and the
	// next state where it looks for events. Any state can return to this state to
	// enable an idle loop.
	case ST_MAIN_SCREEN:

		mState = ST_MAIN_SCREEN_CNT;
		sysMenu = false;
		selectedMenu = 0;
		displayMainScreen();
		break;

	// Main screen state that responds to events. This state is an entry point for
	// the menu structure and allows setting and display of operational variables.
	// Weld pulses are also issued from this state if they are required.
	case ST_MAIN_SCREEN_CNT:

		// Activate a weld pulse if required.
		// Check if AutoPulse is enabled and activated.
		if ( digitalRead( PIN_AUTO_PULSE ) && pData.pFlags.en_autoPulse ) {
			displayMainScreen( 1 );
			sendWeldPulse( PIN_AUTO_PULSE, pData.autoPulseDelay * 100, WP_RETRIGGER_DELAY );
			displayMainScreen();
		}

		// Else check if the Foot switch is activated.
		else if ( !digitalRead( PIN_FOOT_SWITCH ) )
			sendWeldPulse( PIN_FOOT_SWITCH, FS_TRIGGER_DELAY, WP_RETRIGGER_DELAY, PL_ACTIVE_L );

		// A button press event will enter the menu structure.
		if ( mEvent == EV_BTNDN ) {
			mState = ST_MENU_SCREEN;
			selectedMenu = 0;
			mEvent = EV_NONE;
			displayMenuType1( NULL, FPSTR( LS_APULSE ), FPSTR( LS_BATTALM1 ), FPSTR( LS_SHORTPLS1 ), 0 );

		} else {

			// Rotary encoder events will change the value of the weld pulse time.
			// The time is constrained between 1ms and a stored maximum value.
			if ( mEvent == EV_ENCUP || mEvent == EV_ENCDN ) {
				if ( mEvent == EV_ENCUP ) pData.pulseTime = pData.pulseTime < pData.maxPulseTime
			? pData.pulseTime + 1 : pData.maxPulseTime;
				else pData.pulseTime = pData.pulseTime > MIN_PULSE_TIME ?
					               pData.pulseTime - 1 : MIN_PULSE_TIME;

				pData.pulseTime = pData.pulseTime <MIN_PULSE_TIME ? MIN_PULSE_TIME :
				                                   pData.pulseTime> pData.maxPulseTime ? pData.maxPulseTime : pData.pulseTime;
				mEvent = EV_NONE;
			}

			displayMainScreen();
		}

		break;

	// The first menu in the menu structure. This is accessed from the main screen
	// by a button press event.
	case ST_MENU_SCREEN:

		// A button press event will enter the next level of the menu structure. There are
		// three items in the menu to decide which new menu is entered.
		if ( mEvent == EV_BTNDN ) {
			mState = ST_SUB_MENU_1;
			selectedMainMenu = selectedMenu;

			// Enter a sub-menu to select more options.
			if ( selectedMainMenu == 0 )
				displayMenuType1( FPSTR( LS_APULSE ), FPSTR( LS_MANAUTO ),
				                  FPSTR( LS_DELAY ),  FPSTR( LS_EXIT ), selectedMenu );

			// Allow setting of battery low alarm voltage.
			else if ( selectedMainMenu == 1 ) displayMenuType2( FPSTR( LS_BATTALM ),
				                                            valStr( str, pData.batteryAlarm, VF_BATTALM ), FPSTR( LS_VOLTAGE ) );

			// Allow setting of pre-heat pulse duration.
			else if ( selectedMainMenu == 2 ) displayMenuType2( FPSTR( LS_SHORTPLS ),
				                                            valStr( str, pData.shortPulseTime, VF_SHTPLS ), FPSTR( LS_PCOF ) );

			mEvent = EV_NONE;
			selectedMenu = 0;

			// Rotary encoder events will allow scrolling through the menu options.
		} else if ( mEvent == EV_ENCUP || mEvent == EV_ENCDN ) {
			if ( mEvent == EV_ENCDN ) selectedMenu = selectedMenu == 0 ? 2 : selectedMenu - 1;
			else selectedMenu = selectedMenu == 2 ? 0 : selectedMenu + 1;

			mEvent = EV_NONE;
			displayMenuType1( NULL, FPSTR( LS_APULSE ), FPSTR( LS_BATTALM1 ),
			                  FPSTR( LS_SHORTPLS1 ), selectedMenu );
		}

		break;

	// Next menu down the menu structure. This is accessed from the
	// first menu by a button press.
	case ST_SUB_MENU_1:

		// A button press event will enter the next level of the menu structure. There are
		// three items in the menu to decide which new menu is entered.
		if ( mEvent == EV_BTNDN ) {
			if ( selectedMainMenu == 0 ) {
				mState = ST_SUB_MENU_2;
				selectedSubMenu = selectedMenu;

				// Set the auto-pulse status.
				if ( selectedSubMenu == 0 ) displayMenuType2( FPSTR( LS_AUTOPLSON ), NULL,
					                                      pData.pFlags.en_autoPulse ? FPSTR( LS_AUTO ) : FPSTR( LS_MANUAL ) );

				// Allow setting of the auto-pulse delay time.
				else if ( selectedSubMenu == 1 ) displayMenuType2( FPSTR( LS_AUTOPLSDLY ),
					                                           valStr( str, pData.autoPulseDelay, VF_DELAY ), FPSTR( LS_SECONDS ) );
				else if ( selectedSubMenu == 2 ) mState = ST_MAIN_SCREEN;

			} else if ( selectedMainMenu == 1 ) mState = ST_MAIN_SCREEN;

			else if ( selectedMainMenu == 2 ) mState = ST_MAIN_SCREEN;
			else mState = ST_MAIN_SCREEN;

			mEvent = EV_NONE;
			selectedMenu = 0;

			// The menu entry type has already been selected from the previous menu. Here the
			// variables are altered according to the selected type.
		} else if ( mEvent == EV_ENCUP || mEvent == EV_ENCDN ) {
			if ( selectedMainMenu == 0 ) {
				if ( mEvent == EV_ENCDN ) selectedMenu = selectedMenu == 0 ? 2 : selectedMenu - 1;
				else selectedMenu = selectedMenu == 2 ? 0 : selectedMenu + 1;

				displayMenuType1( FPSTR( LS_APULSE ), FPSTR( LS_MANAUTO ),
				                  FPSTR( LS_DELAY ),  FPSTR( LS_EXIT ), selectedMenu );

				// Set the battery alarm voltage by responding to rotary encoder events.
				// The battery alarm voltage cannot be set higher than the current battery voltage
				// and in any event not higher than the maximum allowable alarm voltage.
			} else if ( selectedMainMenu == 1 ) {
				if ( mEvent == EV_ENCDN ) pData.batteryAlarm = pData.batteryAlarm >
					                                       MIN_BATT_BALARM ? pData.batteryAlarm - 1 : MIN_BATT_BALARM;
				else pData.batteryAlarm = pData.batteryAlarm < min( batteryVoltage, MAX_BATT_ALARM ) ?
					                  pData.batteryAlarm + 1 : min( batteryVoltage, MAX_BATT_ALARM );

				displayMenuType2( FPSTR( LS_BATTALM ),
				                  valStr( str, pData.batteryAlarm, VF_BATTALM ), FPSTR( LS_VOLTAGE ) );

				// Set the pre-heat pulse duration by responding to rotary encoder events.
			} else if ( selectedMainMenu == 2 ) {
				if ( mEvent == EV_ENCDN ) pData.shortPulseTime = pData.shortPulseTime >
					                                         MIN_SPULSE_TIME ?  pData.shortPulseTime - 1 : MIN_SPULSE_TIME;
				else pData.shortPulseTime = pData.shortPulseTime < MAX_SPULSE_TIME ?
					                    pData.shortPulseTime + 1 : MAX_SPULSE_TIME;

				displayMenuType2( FPSTR( LS_SHORTPLS ),
				                  valStr( str, pData.shortPulseTime, VF_SHTPLS ), FPSTR( LS_PCOF ) );
			}

			mEvent = EV_NONE;
		}

		break;

	case ST_SUB_MENU_2:

		if ( mEvent == EV_BTNDN ) {
			mState = ST_MAIN_SCREEN;
			mEvent = EV_NONE;
			selectedMenu = 0;
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

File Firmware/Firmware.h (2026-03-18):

#ifndef _ARDUINO_SPOT_WELDER_V3_H
#define _ARDUINO_SPOT_WELDER_V3_H
/***********************************************************************************************/ /**
 *  \par        Arduino Spot Welder - Header.
 *
 *  \par        Details
 *  \par
 *              Arduino Spot Welder V3 firmware.
 *              This is the Arduino Code for the Spot Welder V3. Do not use it with the older V2 
 *              pcbs. It is not compatible with these.
 *  \par
 *              You need to have the Adafruit_GFX library and the Adafruit_SSD1306 library 
 *              installed in your Arduino IDE to sucessfully compile the Code.
 *              
 *              This release has been tested with the following library versions:    
 *              Adafruit SSD1306 V2.5.13
 *              Adafruit GFX V1.12.0           
 *
 *  \file       Arduino_Spot_Welder_V3_3_5.h
 *  \author     Marc Schönfleisch <http://malectrics.eu/>
 *  \version    3.3.5
 *  \date       April 2025
 *  \copyright  Copyright(c)2025 Marc Schönfleisch <info@malectrics.eu>. All right reserved.
 *
 *  \par        Changelog
 *  \li         01jul2017  MS  Initial release
 *  \li         12dec2017  JFF New release with major rewrite
 *  \li         15djan2018  MS change battery voltage reading for V3.2 Spot Welder 
 *  \li         05djun2018  MS remove softwarereset to eliminate need of optiboot bootloader 
 *  \li         11aug2018  MS fix 10.000 welds counter bug
 *  \li         24nov2018  AJ improve Auto Pulse functionality with progress bar
 *  \li         09apr2019  MS add foot switch wrong connection error message
 *  \li         05jun2019  MS code update for SSD1306 library V1.2.9 and general improvements
 *  \li         12sep2019  GW imporove slow progress bar drawing problem
 *  \li         01apr2020  RS fix 10.000 welds count limit
 *  \li         03apr2020  MS add overvoltage alarm  
 *  \li         09apr2025  MS improve measured voltage offset calibration
 *
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
 */
                                                                                                  /***********************************************************************************************/

// General macros
#define str(s) #s
#define xstr(s) str(s)

// Most of these macros define strings that appear on the splash screen
// (each line of the splash screen is limited to 21 characters)
#define _DEVICENAME_ "Arduino Spot Welder"
#define _PROGNAME_ "Arduino Spot Welder Control Firmware"
#define _AUTHOR_ "Marc Schonfleisch"
#define _VERSION_MAJOR_ 3
#define _VERSION_MINOR_ 3
#define _REVISION_ 5
#define _COPYRIGHT_ "2025"
#define _COMPANY_ "Malectrics"
#define _RIGHTS_ "All right reserved"

/***************************************************************************************************
* User Configuration                                                                               *
***************************************************************************************************/

//#define _DEVELOPMENT_                       /**< Allows printing of diagnostics */
//#define _BOOTSYS_                           /**< Force boot to system menu for testing */

#define _LANG_EN_ /**< Language:  _LANG_EN/DE/FR/ES/IT_ */
//#define _TESTING_                           /**< Allows ignoring the low battery alarm */
#define _SERIAL_BAUD_ 115200 /**< Comms rate for serial debugging */

/***************************************************************************************************
* Pin and interrupt definitions                                                                    *
***************************************************************************************************/

#define ENC_INT 0         /**< Rotary interrupt for CLK input (Ph0) */
#define PIN_CLK 2         /**< Rotary encoder CLK input (Ph0) */
#define PIN_DT 8          /**< Rotary encoder DT input (Ph1) */
#define PIN_SW 6          /**< Rotary encoder push button switch input */
#define PIN_FOOT_SWITCH 7 /**< Foot switch sense input */
#define PIN_AUTO_PULSE 3  /**< Auto-pulse sense input */
#define PIN_PULSE 5       /**< Weld pulse output */
#define PIN_LED 4         /**< Status LED output */
#define PIN_BATT_V A0     /**< A/D input for battery voltage sense */

/***************************************************************************************************
* Macros                                                                                           *
***************************************************************************************************/
// Defaults for operational variables
#define DEF_AUTO_PLSDELAY 20    /**< Default auto pulse delay time (ms*100) */
#define DEF_PULSE_TIME 5        /**< Default pulse time (ms) */
#define DEF_MAX_PULSE_TIME 100  /**< Default maximum pulse time (ms) */
#define DEF_SPULSE_TIME 12      /**< Default short pulse time (% of pulse time) */
#define DEF_NOM_BATT_V 124      /**< Default nominal battery voltage (for testing) */
#define DEF_MAX_BATT_V 127      /**< Default maximum battery voltage (V*10) */
#define DEF_PULSE_VOLTAGE 40    /**< Default voltage during pulse (for testing) (V*10) */
#define DEF_PULSE_AMPS 5000     /**< Default Amps during pulse (for testing) (A*10) */
#define DEF_BATTERY_OFFSET 0    /**< Default battery calibration offset (V*10) */
#define DEF_BATT_ALARM 110      /**< Default low battery voltage (V*10) */
#define DEF_HIGH_BATT_ALARM 145 /**< Default high battery voltage (V*10) */
#define DEF_AUTO_PULSE true     /**< Default Auto-pulse enable */
#define DEF_OLED_INVERT false   /**< Default OLED orientation */

// Limits for operational variables
#define MIN_PULSE_TIME 1    /**< Minimum weld pulse time */
#define MAX_PULSE_TIME 500  /**< Absolute maximum weld pulse time */
#define MAX_APULSE_DELAY 50 /**< Maximum auto pulse delay */
#define MIN_APULSE_DELAY 5  /**< Minimum auto pulse delay */
#define MAX_SPULSE_TIME 100 /**< Maximum short pulse time */
#define MIN_SPULSE_TIME 0   /**< Minimum short pulse time */
#define MAX_BATT_ALARM 120  /**< Maximum low battery alarm voltage */
#define MIN_BATT_BALARM 74  /**< Minimum low battery alarm voltage */
#define MAX_BATT_V 200      /**< Absolute maximum battery voltage */
#define MIN_BATT_V 50       /**< Absolute minimum battery voltage */

// Timing macros
#define STANDBY_TIME_OUT 300000L /**< Device sleep timeout (ms) */
#define EEPROM_UPDATE_T 5000     /**< EEPROM update time (ms) */
#define WP_RETRIGGER_DELAY 500   /**< Weld pulse re-trigger delay (ms) */
#define FS_TRIGGER_DELAY 200     /**< Foot switch activation delay (ms) */
#define RS_DEBOUNCE 50 /*20*/    /**< Rotary encoder & switch debounce time (ms) */
#define BV_INTERVAL 20000        /**< Battery voltage measurement interval (ms) */
#define PV_DELAY 2000            /**< Time the foot switch has to be hold before the pulse data is shown after a pulse (ms) */
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

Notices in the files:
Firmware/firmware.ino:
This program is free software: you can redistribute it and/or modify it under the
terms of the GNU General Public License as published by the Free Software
